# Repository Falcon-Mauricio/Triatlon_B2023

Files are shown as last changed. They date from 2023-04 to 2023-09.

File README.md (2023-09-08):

# Triatlon_B2023

### Indice
[PINOUT PCB](#pinout)<br>
[Normas de convivencia de codigo](#normas)<br>
[Organizacion del repositorio y colaboracion](#colab)<br>
[Imagenes](#imag)<br>

## PINOUT PCB

### Kairimi
```
// Motores
#define M2A 22
#define M2B 23
#define M1B 19
#define M1A 21

// Sensores
#define SENSOR_1 13
#define SENSOR_2 27
#define SENSOR_3 26
#define SENSOR_4 25
#define SENSOR_5 34
#define SENSOR_6 35
#define SENSOR_7 32
#define SENSOR_8 33
#define LEFT_CNY 27
#define RIGHT_CNY 25
#define BACK_CNY 26

// Control
#define BUZZER 18
#define PUSH_1 16
#define PUSH_2 17
```

### C5
```
#define SENSOR_1 13 // left side sharp  
#define SENSOR_2 27 // back cny
#define SENSOR_3 26 // right side sharp
#define SENSOR_4 25 // right cny
#define SENSOR_5 34 // left cny
#define SENSOR_6 35 // left sharp
#define SENSOR_7 32 // center sharp
#define SENSOR_8 33 // right sharp

```
<br>

## Normas de convivencia de codigo

* #### 1.  Convencion de nomenclatura:

    | Tipo      | Caso           | Ejemplo      |
    | :-------: |:--------------:|:------------:|
    | constantes| screaming snake|MAX_READING   |
    | variables | snake case     |color_deadline|
    | objetos   | snake case     |left_sharp    |
    | clases    | pascal case    |Motor         |
    | funciones | pascal case    |ReadFloor     |

* #### 2.  Orden del codigo:

    * Importar librerias
    * Definicion pines
    * Definicion de constantes / variables globales
    * Creacion de clases / objetos (hasta terminar la modularizacion)
    * Funciones globales
    * Velocista
    * Sumo radiocontrolado
    * Despejar area
    * Seleccion de modo / setup / loop
    
* #### 3. Legibilidad:

    * Usar define para los numeros aislados
    * Comentarios descriptivos
    * Codigo limpio y ordenado

<br>

## Organizacion del repositorio y colaboracion

### Arbol de carpetas:

```
├───C5
│   ├───3D
│   ├───CODE
│   └───PCB
├───Kairimi
│   ├───3D
│   ├───CODE
│   └───PCB
├───resources
└───shared
    ├───examples
    └───libs
```

* C5: Dedicado a la version C5 (Rodri/Mauri)

* Kairimi: Dedicado a la version Kairimi (Iris/Julian).
* resources: Librerias externas necesarias para correr el codigo
* shared: Archivos compartidos para los dos robots, como librerias dedicadas

### Colaboracion:

Para colaborar es preferible forkear el repositorio, editar lo necesario en el momento y enviar un pull request. Esto para mantener la actualizacion de archivos ordenada y evitar conflictos entre los robots.

Cuando se alcance una version funcional del robot tagerla marcando las diferencias y mejoras respecto a la anterior y tiempos records de pistas.

<br>

## Imagenes 3Ds / PCBs

### KAIRIMI:

(https://postimg.cc/2q26kCcF)

### C5:

3d en desarrollo.

# Manolos ahi voy 🤤

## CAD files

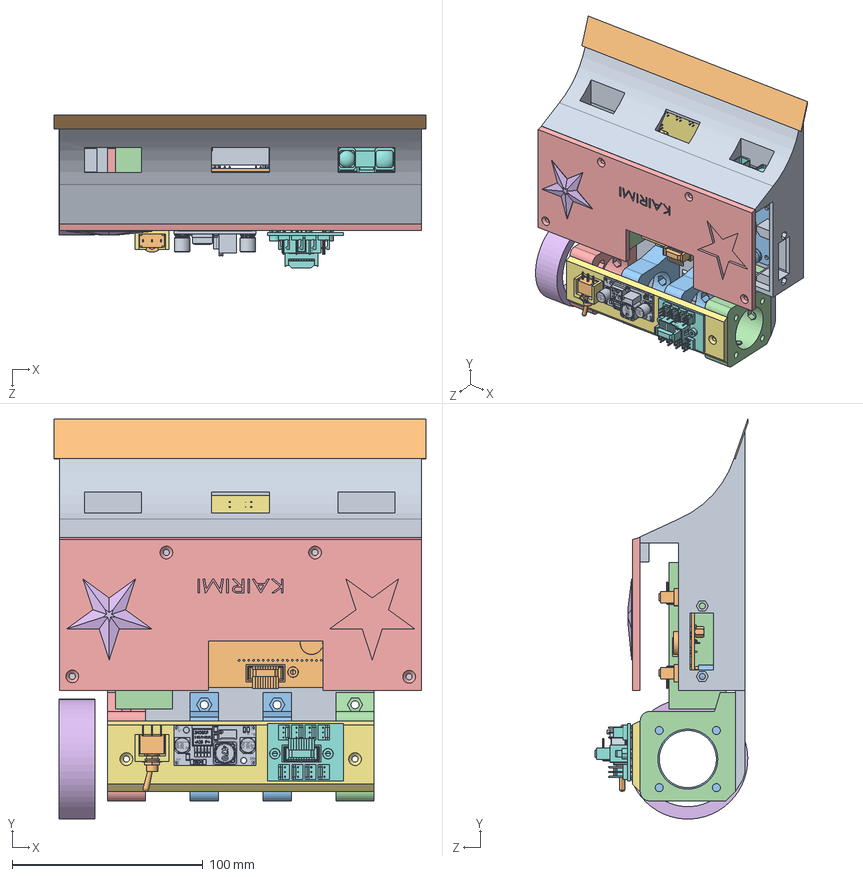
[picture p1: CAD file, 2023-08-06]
C5/3D/Chasis_B2023.SLDASM
195.0 x 209.9 x 80.1 mm
Chasis_B2023_V1
Cuchilla_Fina
Abrazadera_motores_APYS x 2
Soporte_motores_APYS_DER
Soporte_motores_APYS_IZQ
Cubierta_Lisa

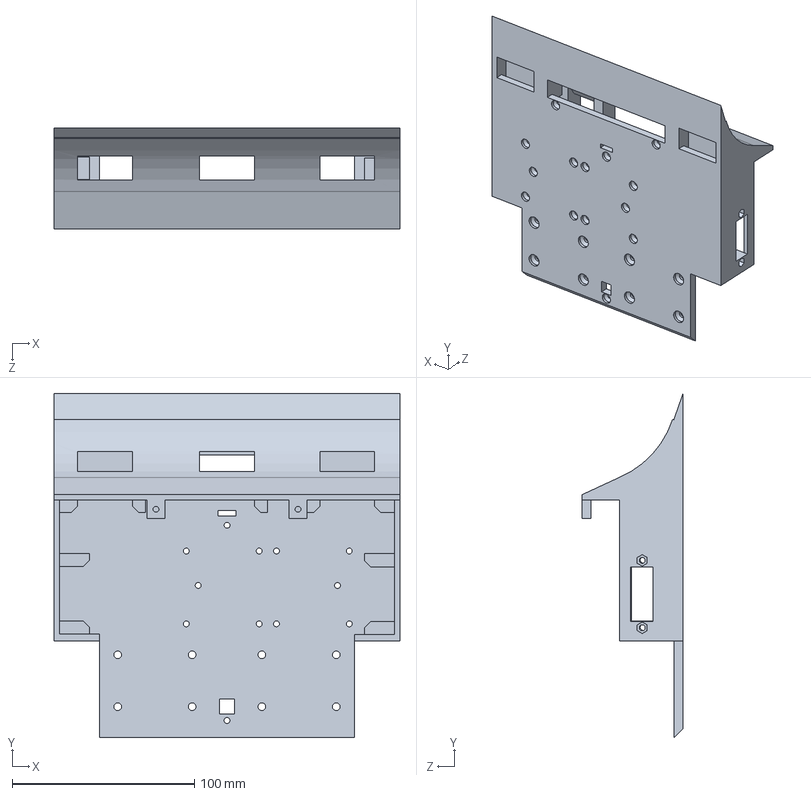
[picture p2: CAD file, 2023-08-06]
C5/3D/Chasis_B2023_V1.SLDPRT
190.0 x 189.1 x 55.5 mm

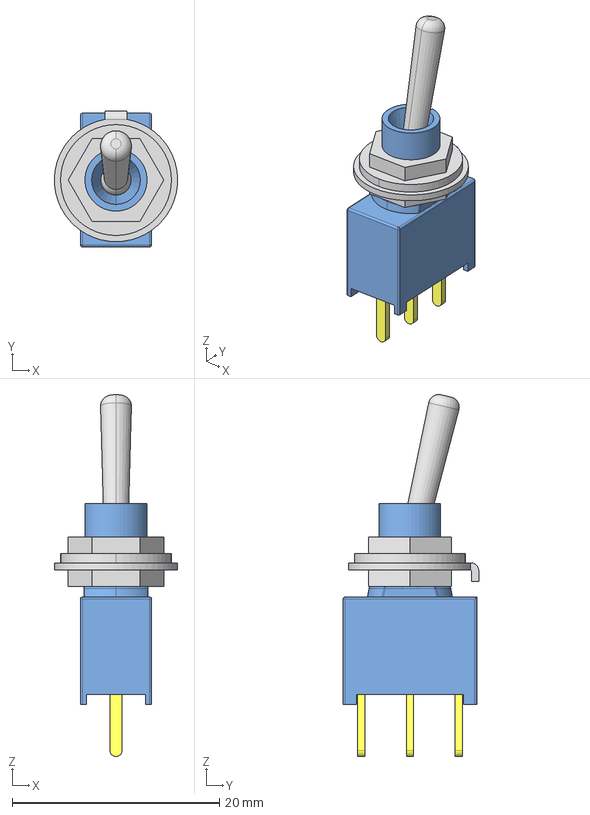
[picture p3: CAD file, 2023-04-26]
C5/3D/Bateria_5V/SW_SPDT_TH_VERTICAL.step
11.9 x 13.1 x 34.9 mm

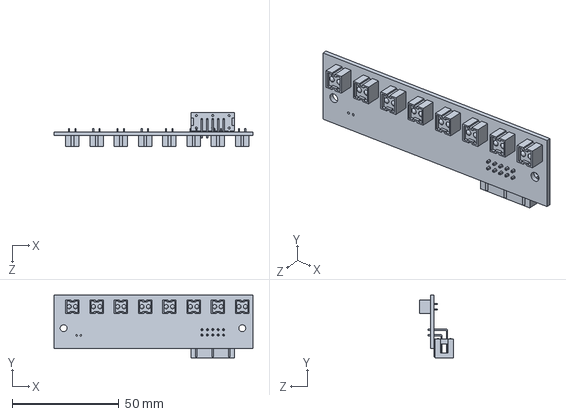
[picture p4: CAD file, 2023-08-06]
C5/3D/PCB_Line_Sensors_x8V2.SLDPRT
93.0 x 29.4 x 16.1 mm

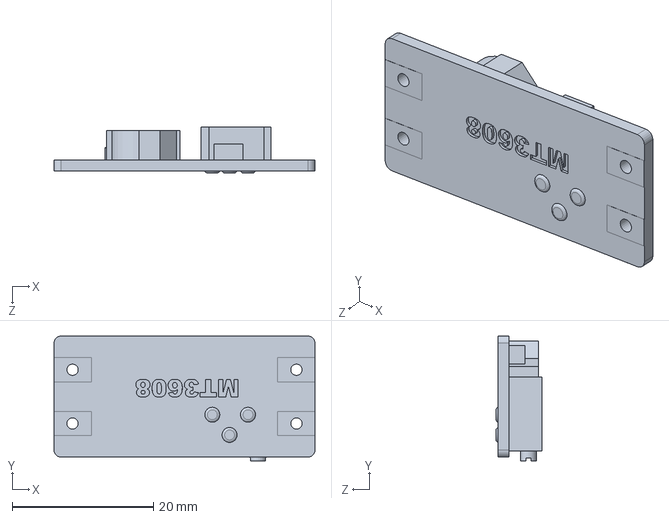
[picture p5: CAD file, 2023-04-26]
C5/3D/Bateria_5V/MT3608_Module_762.SLDPRT
37.0 x 17.7 x 6.50 mm

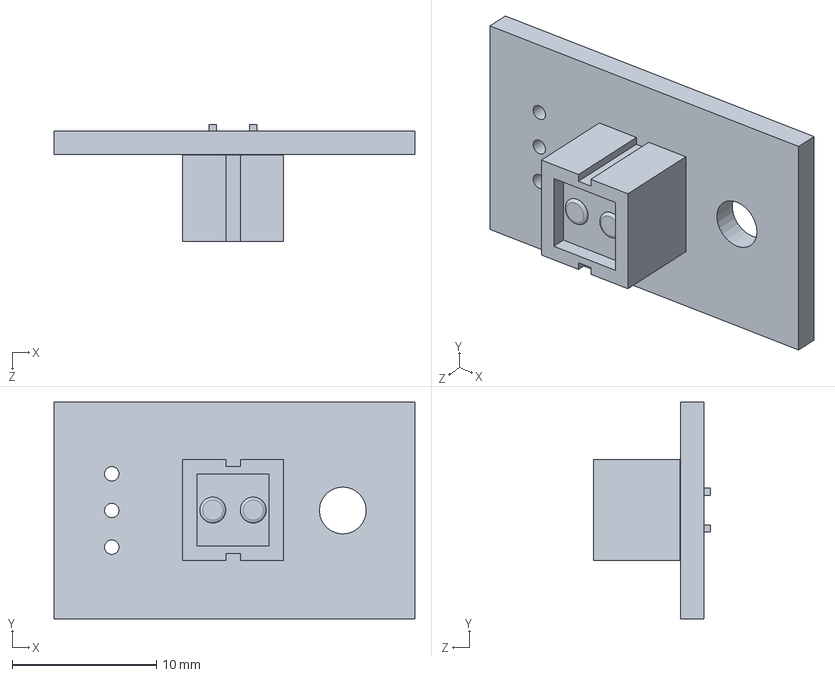
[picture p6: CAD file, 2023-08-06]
C5/3D/PCB_CNY70.SLDPRT
25.0 x 15.0 x 8.12 mm

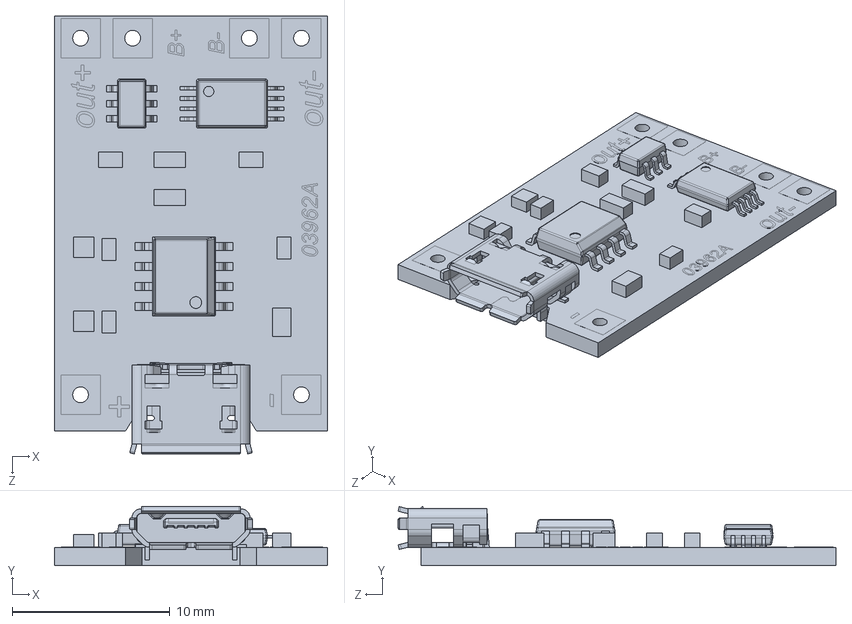
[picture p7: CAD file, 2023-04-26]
C5/3D/Bateria_5V/TP4056.SLDPRT
17.3 x 3.76 x 27.8 mm

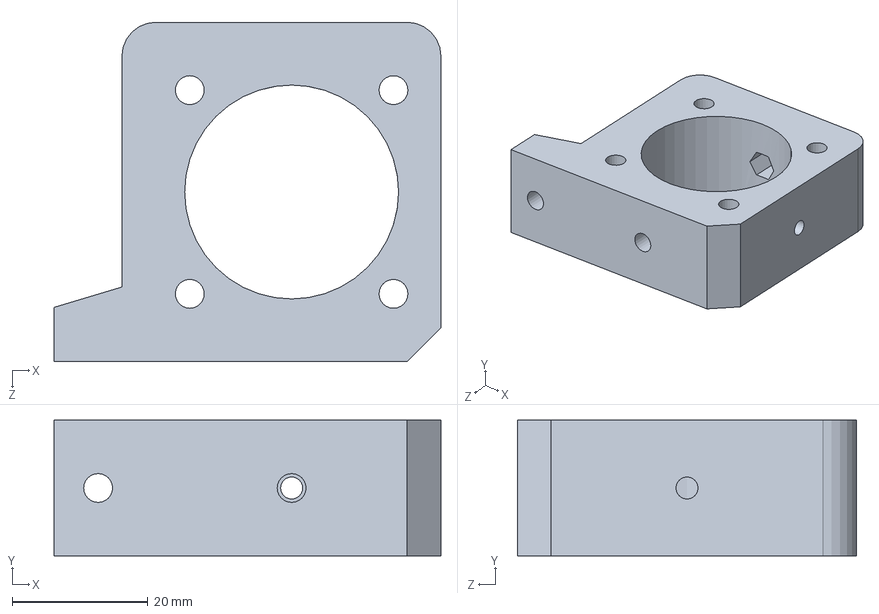
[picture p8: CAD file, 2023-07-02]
C5/3D/Soporte_motores_APYS_IZQ.SLDPRT
57.0 x 20.0 x 50.0 mm

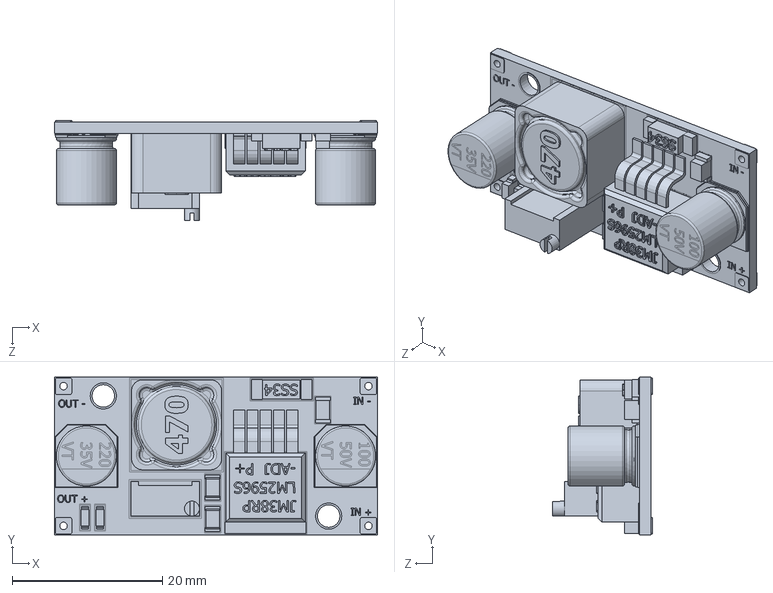
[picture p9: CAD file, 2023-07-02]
C5/3D/lm2596.SLDPRT
43.0 x 21.0 x 13.4 mm

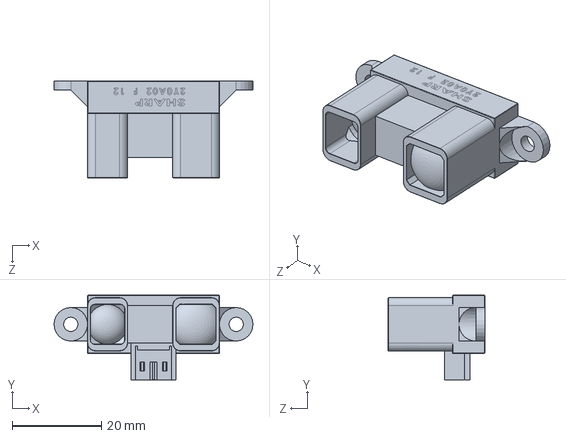
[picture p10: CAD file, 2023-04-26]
C5/3D/GP2Y0A02YK0F_SHARP.SLDPRT
44.5 x 18.9 x 21.6 mm

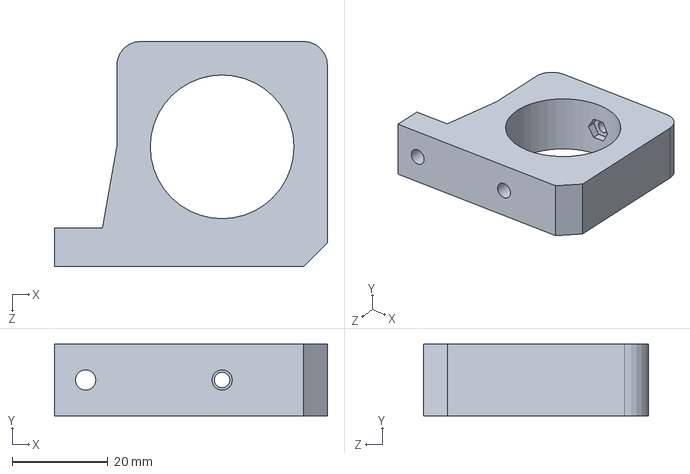
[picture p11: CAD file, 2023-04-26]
C5/3D/Abrazadera_motores_APYS.SLDPRT
57.0 x 15.0 x 47.0 mm

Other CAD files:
C5/3D/Bateria_5V/Base_5v_usb.SLDPRT
C5/3D/Tapa_B2023.SLDPRT
C5/3D/Estrella_Tapa.SLDPRT
C5/3D/Soporte_Alimentacion.SLDPRT
C5/3D/Soporte_SensorMedio.SLDPRT
C5/3D/Cubierta_Lisa.SLDPRT
C5/3D/Soporte_motores_APYS_DER.SLDPRT
C5/3D/BTS7960.SLDPRT
C5/3D/Bateria 4s.SLDPRT
C5/3D/Bateria_5V/18650_Holder.SLDPRT
C5/3D/Cuchilla_Fina.SLDPRT

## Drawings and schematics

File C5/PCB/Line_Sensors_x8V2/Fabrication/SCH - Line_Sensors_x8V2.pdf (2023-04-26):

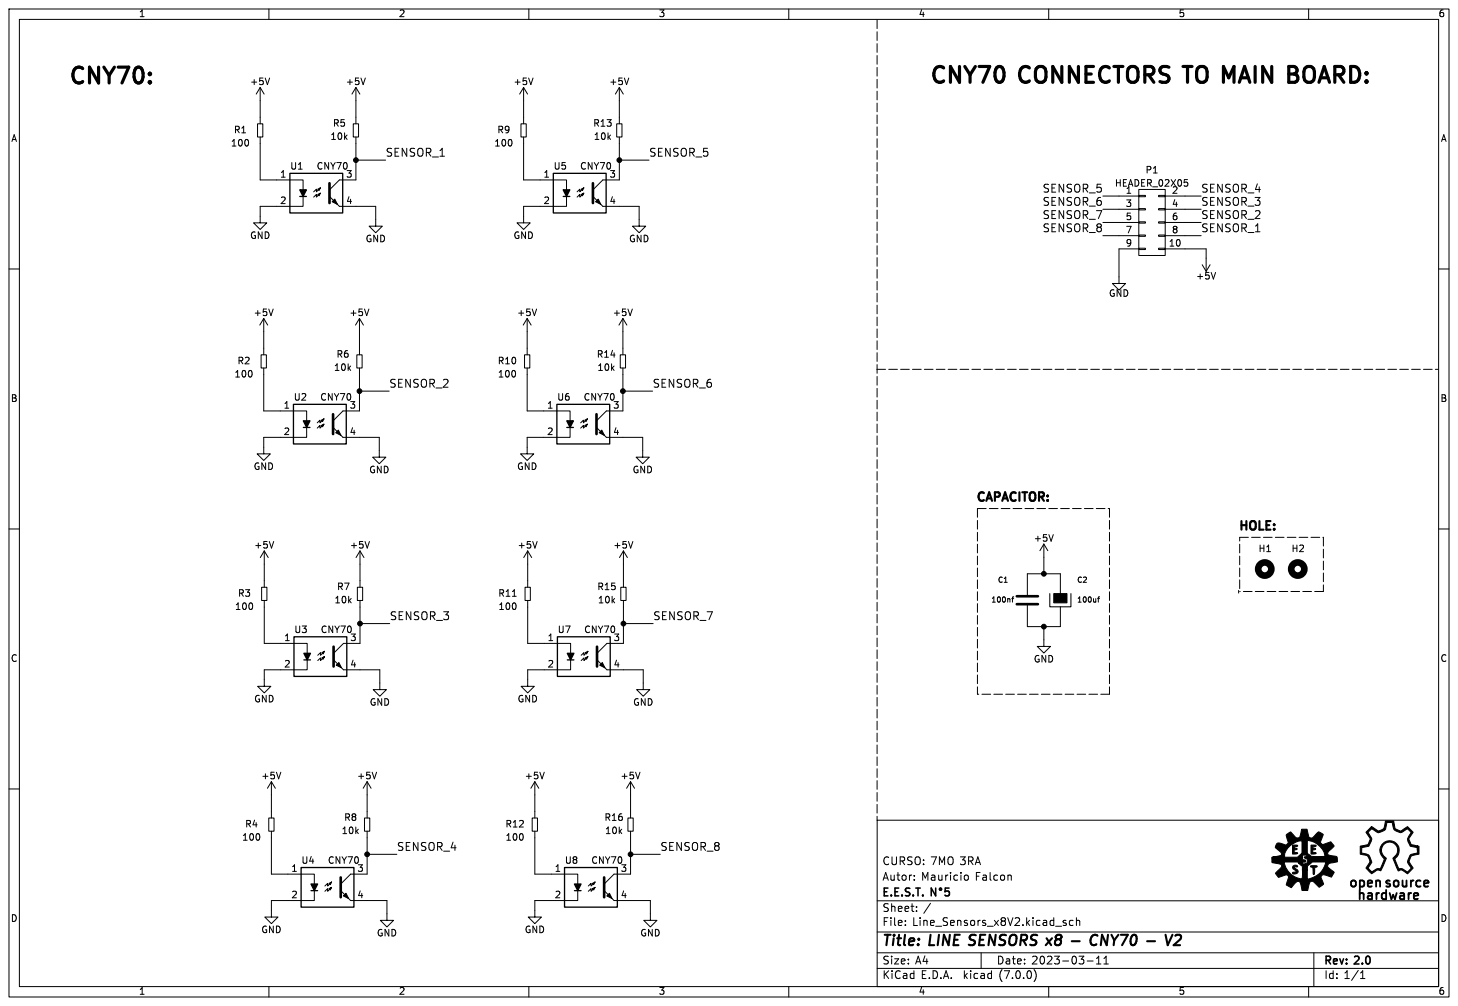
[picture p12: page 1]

CNY70 CONNECTORS TO MAIN BOARD:

Id: 1/1 Title: LINE SENSORS x8 - CNY70 - V2

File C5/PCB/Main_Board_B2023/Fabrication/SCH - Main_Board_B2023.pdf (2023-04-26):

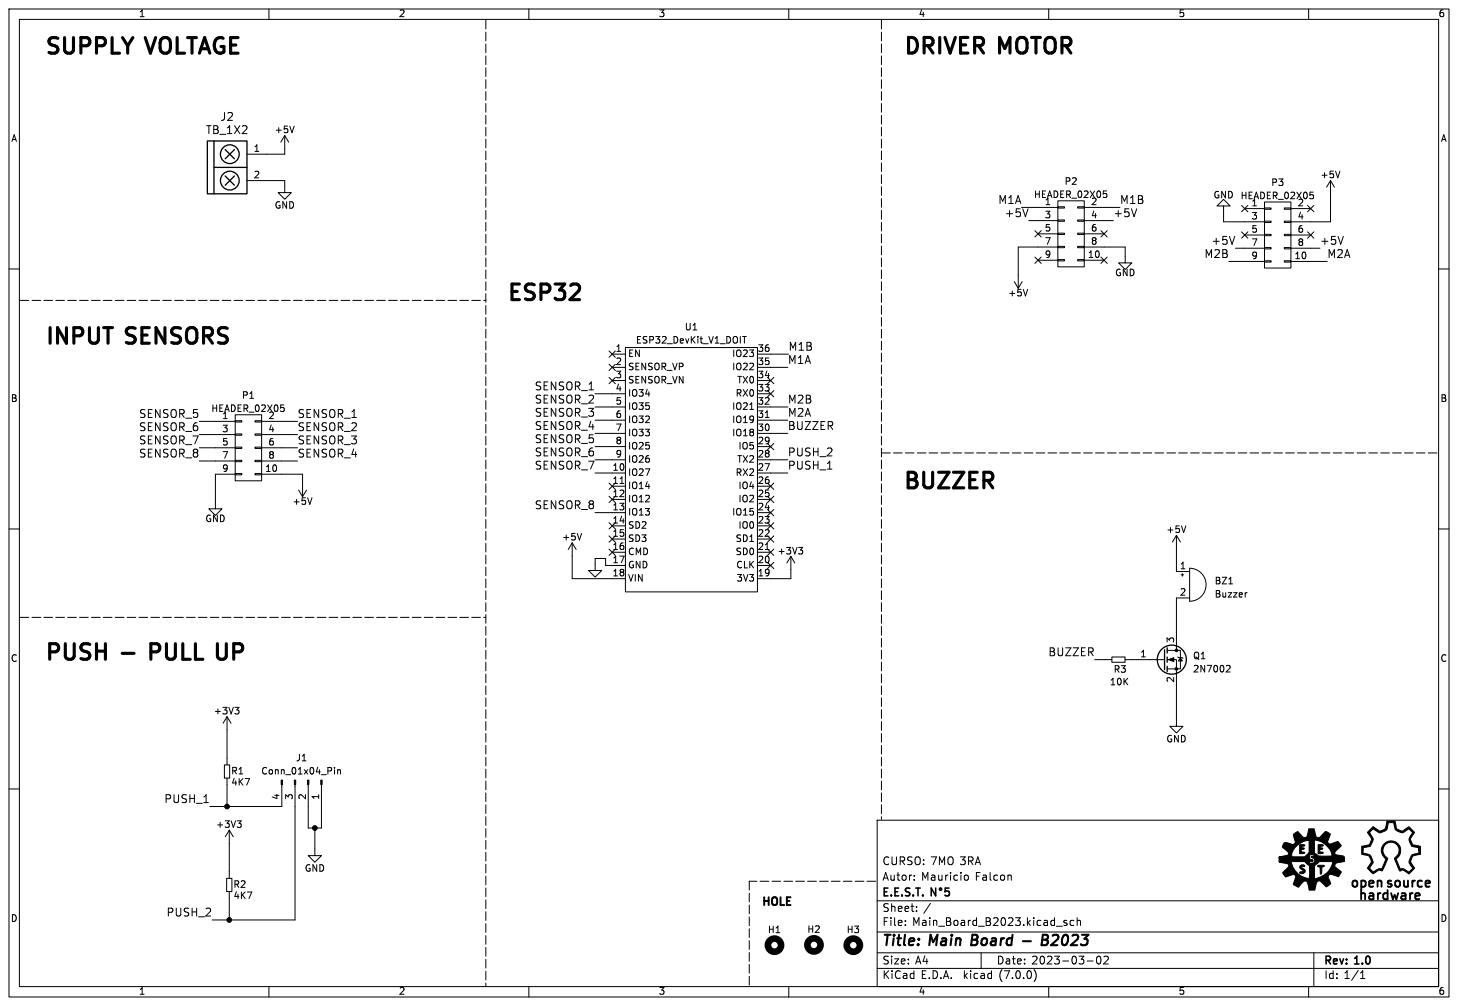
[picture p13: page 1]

Id: 1/1 Title: Main Board - B2023

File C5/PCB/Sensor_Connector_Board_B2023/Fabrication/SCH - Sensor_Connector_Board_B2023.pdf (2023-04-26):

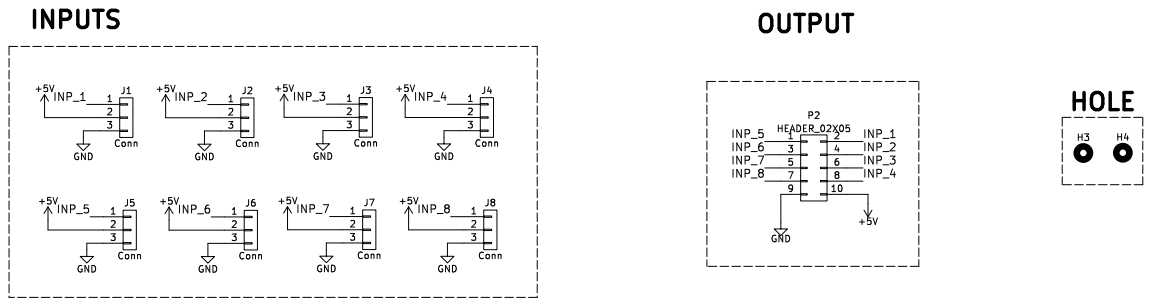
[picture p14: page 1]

Id: 1/1 Title: Sensor Connector Board - B2023

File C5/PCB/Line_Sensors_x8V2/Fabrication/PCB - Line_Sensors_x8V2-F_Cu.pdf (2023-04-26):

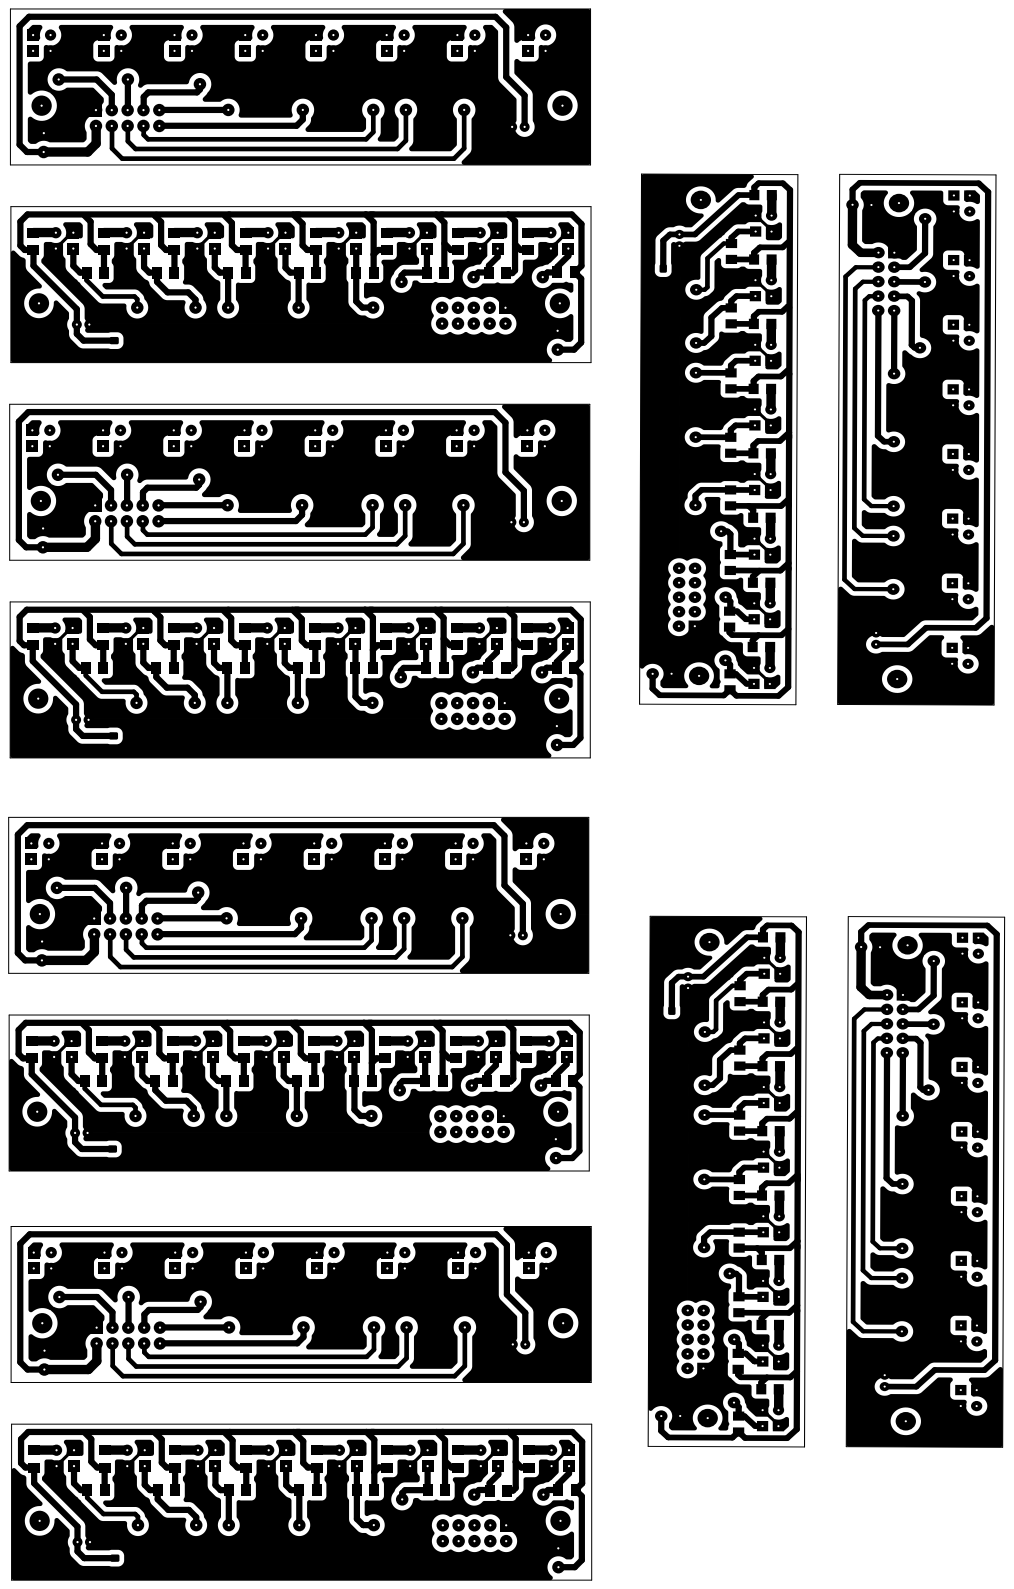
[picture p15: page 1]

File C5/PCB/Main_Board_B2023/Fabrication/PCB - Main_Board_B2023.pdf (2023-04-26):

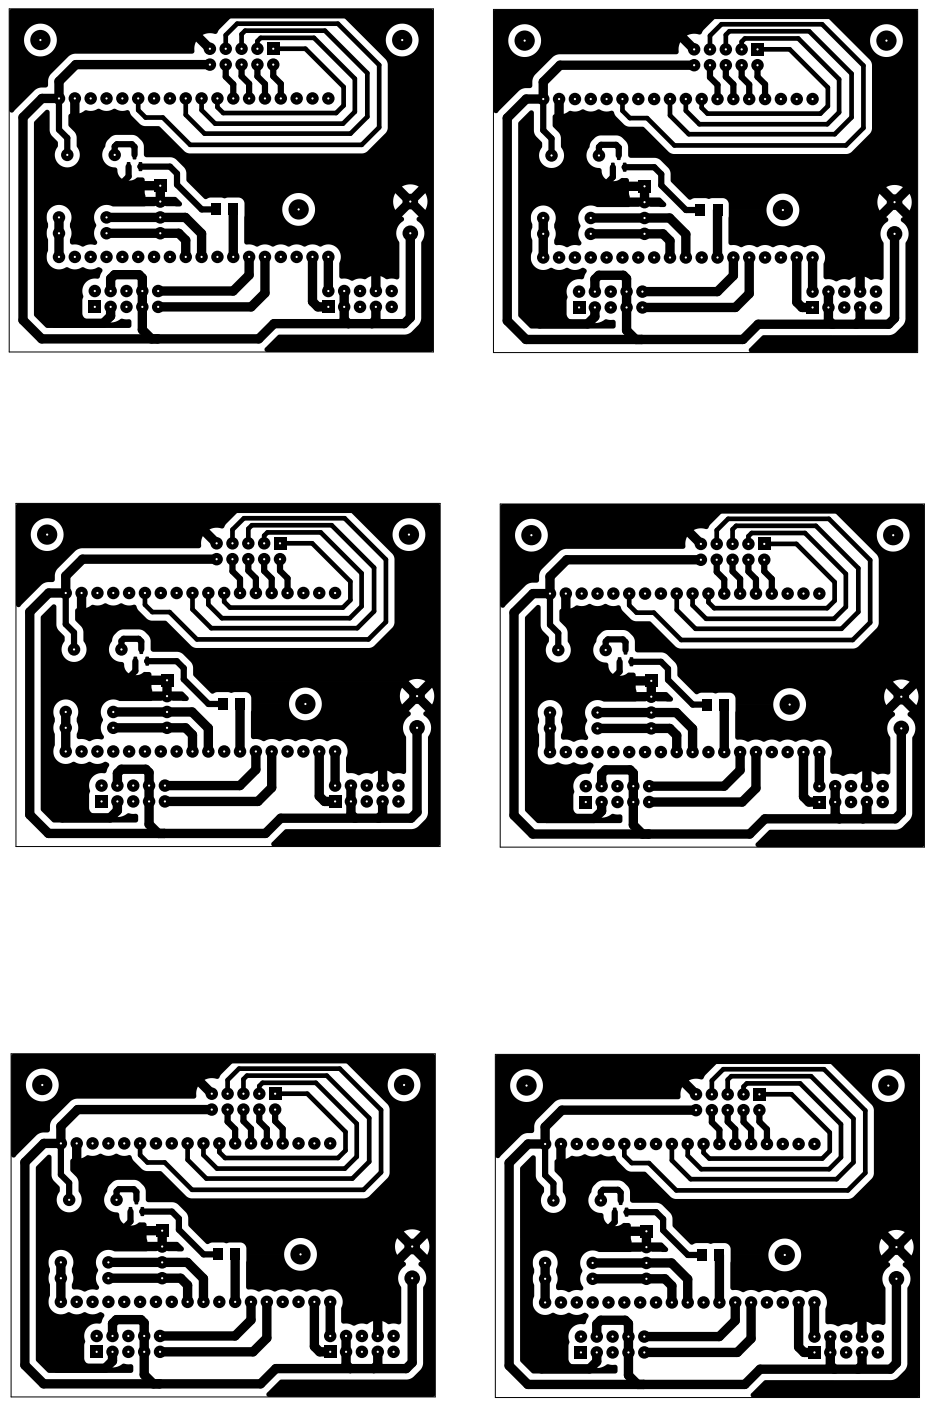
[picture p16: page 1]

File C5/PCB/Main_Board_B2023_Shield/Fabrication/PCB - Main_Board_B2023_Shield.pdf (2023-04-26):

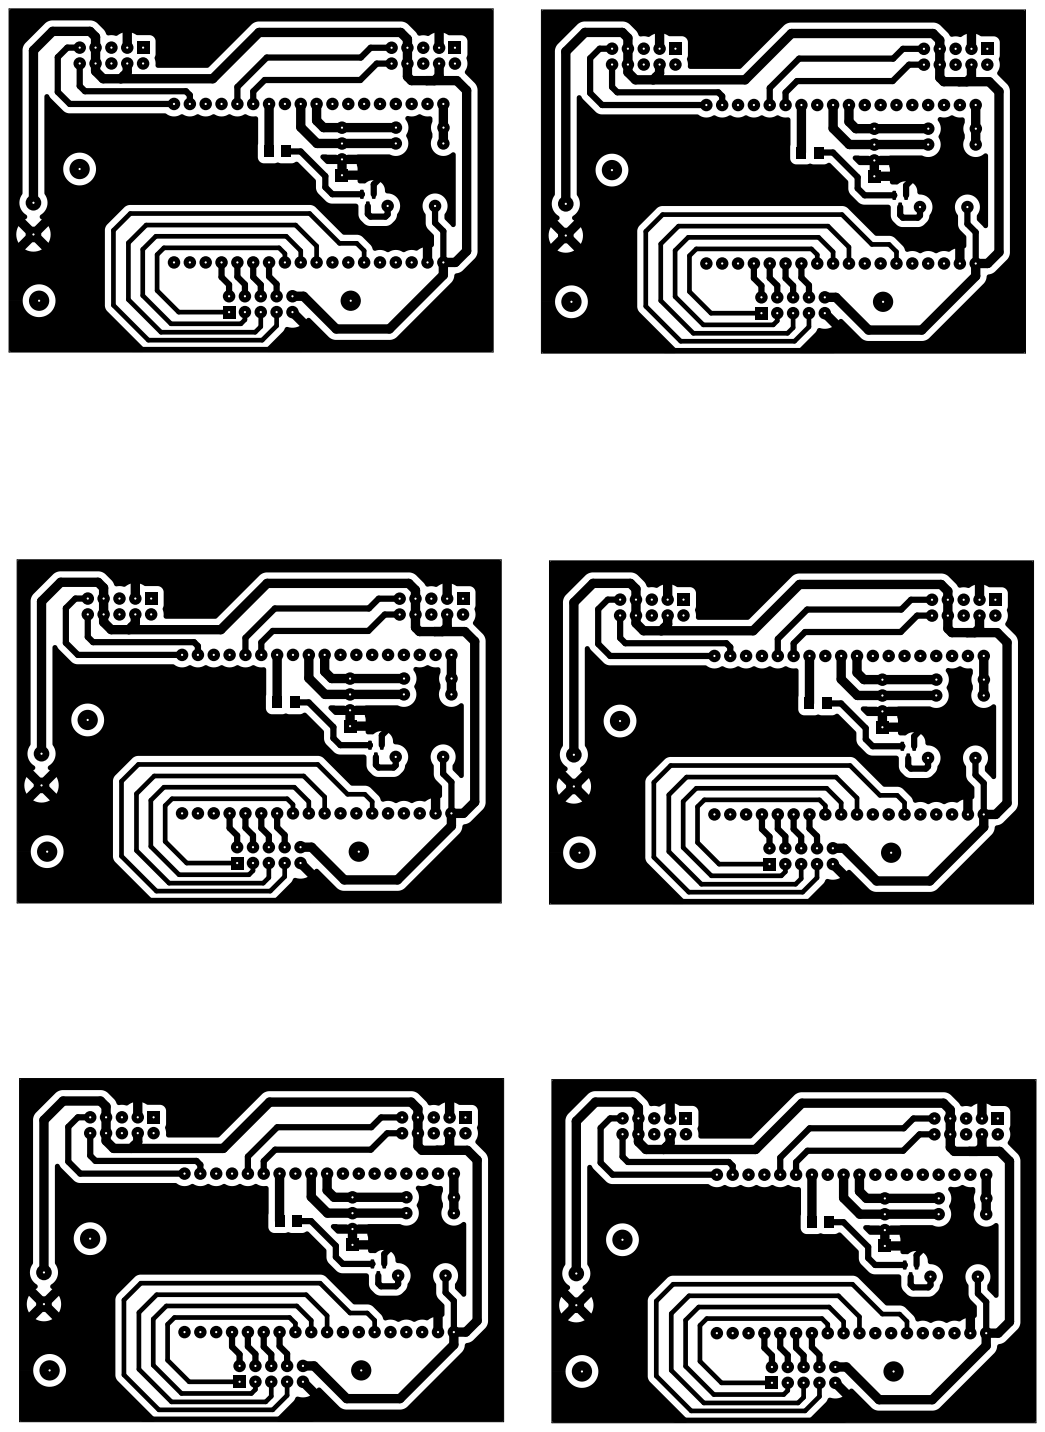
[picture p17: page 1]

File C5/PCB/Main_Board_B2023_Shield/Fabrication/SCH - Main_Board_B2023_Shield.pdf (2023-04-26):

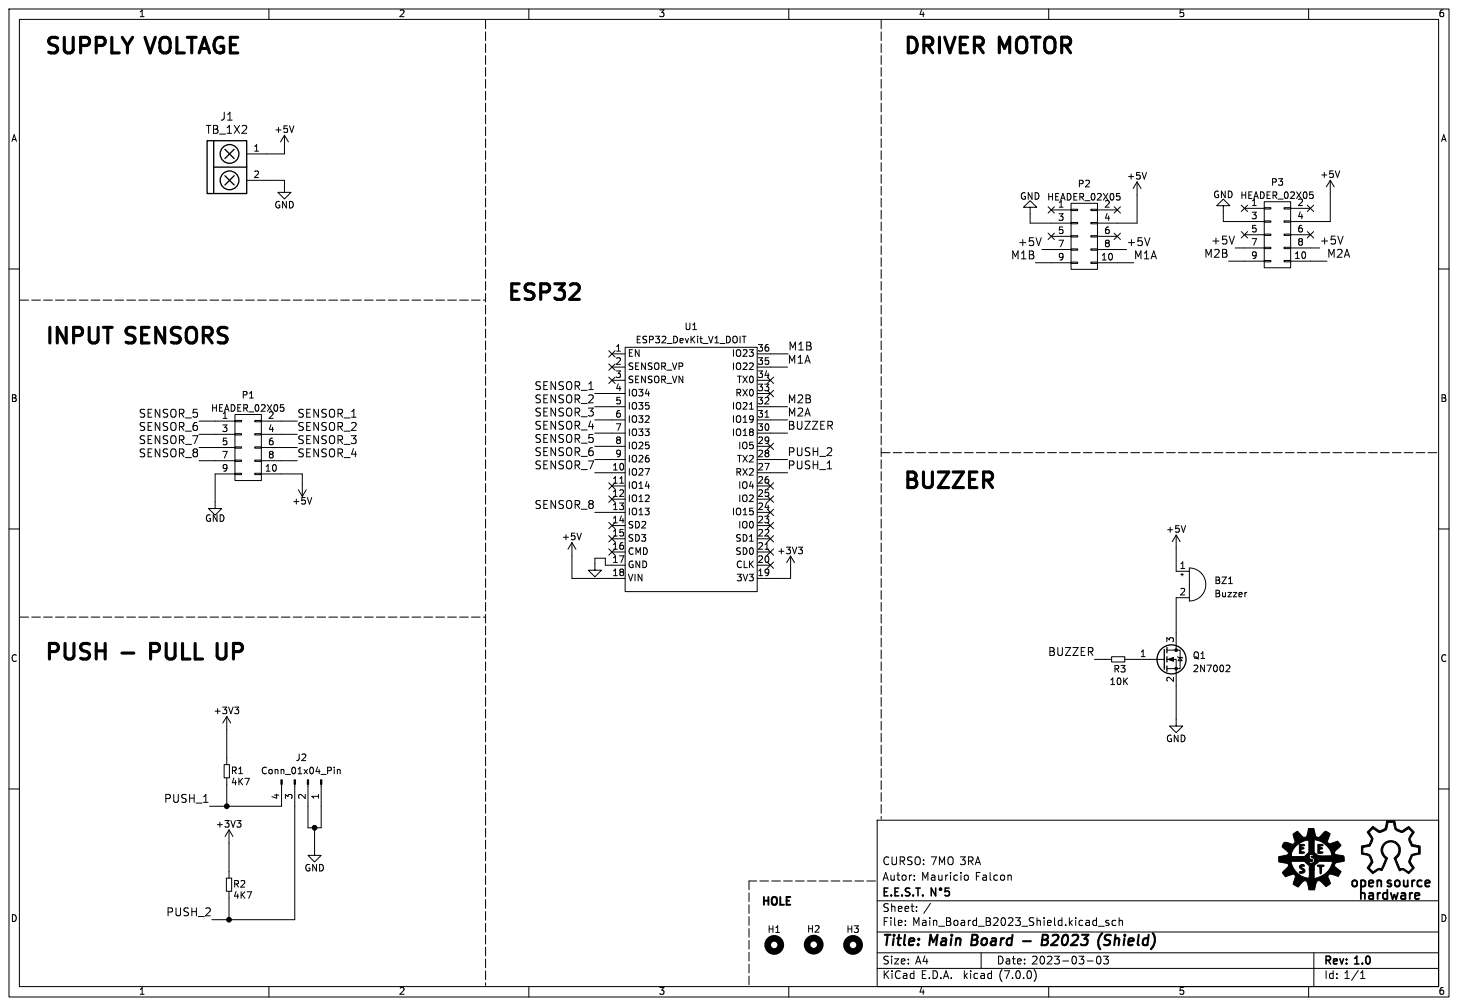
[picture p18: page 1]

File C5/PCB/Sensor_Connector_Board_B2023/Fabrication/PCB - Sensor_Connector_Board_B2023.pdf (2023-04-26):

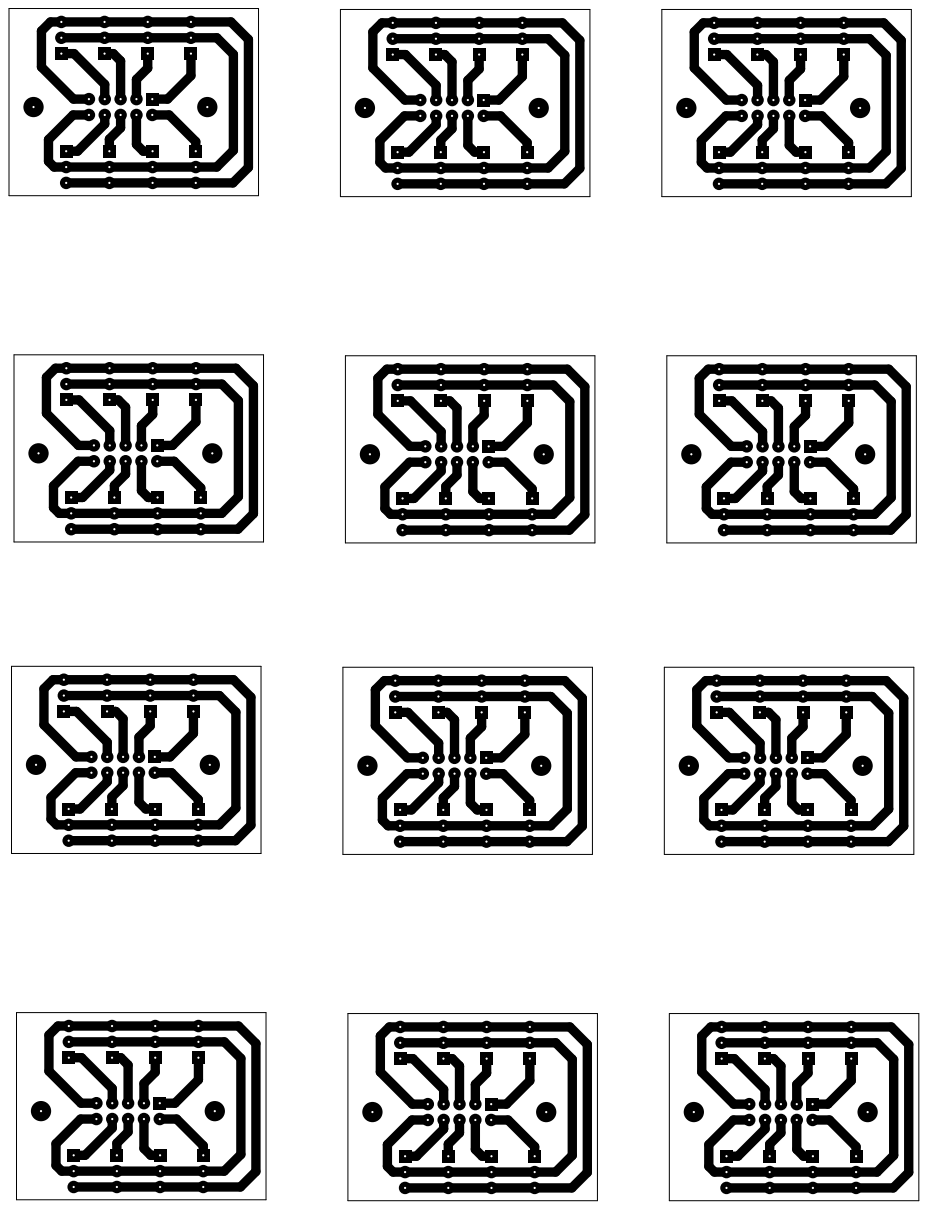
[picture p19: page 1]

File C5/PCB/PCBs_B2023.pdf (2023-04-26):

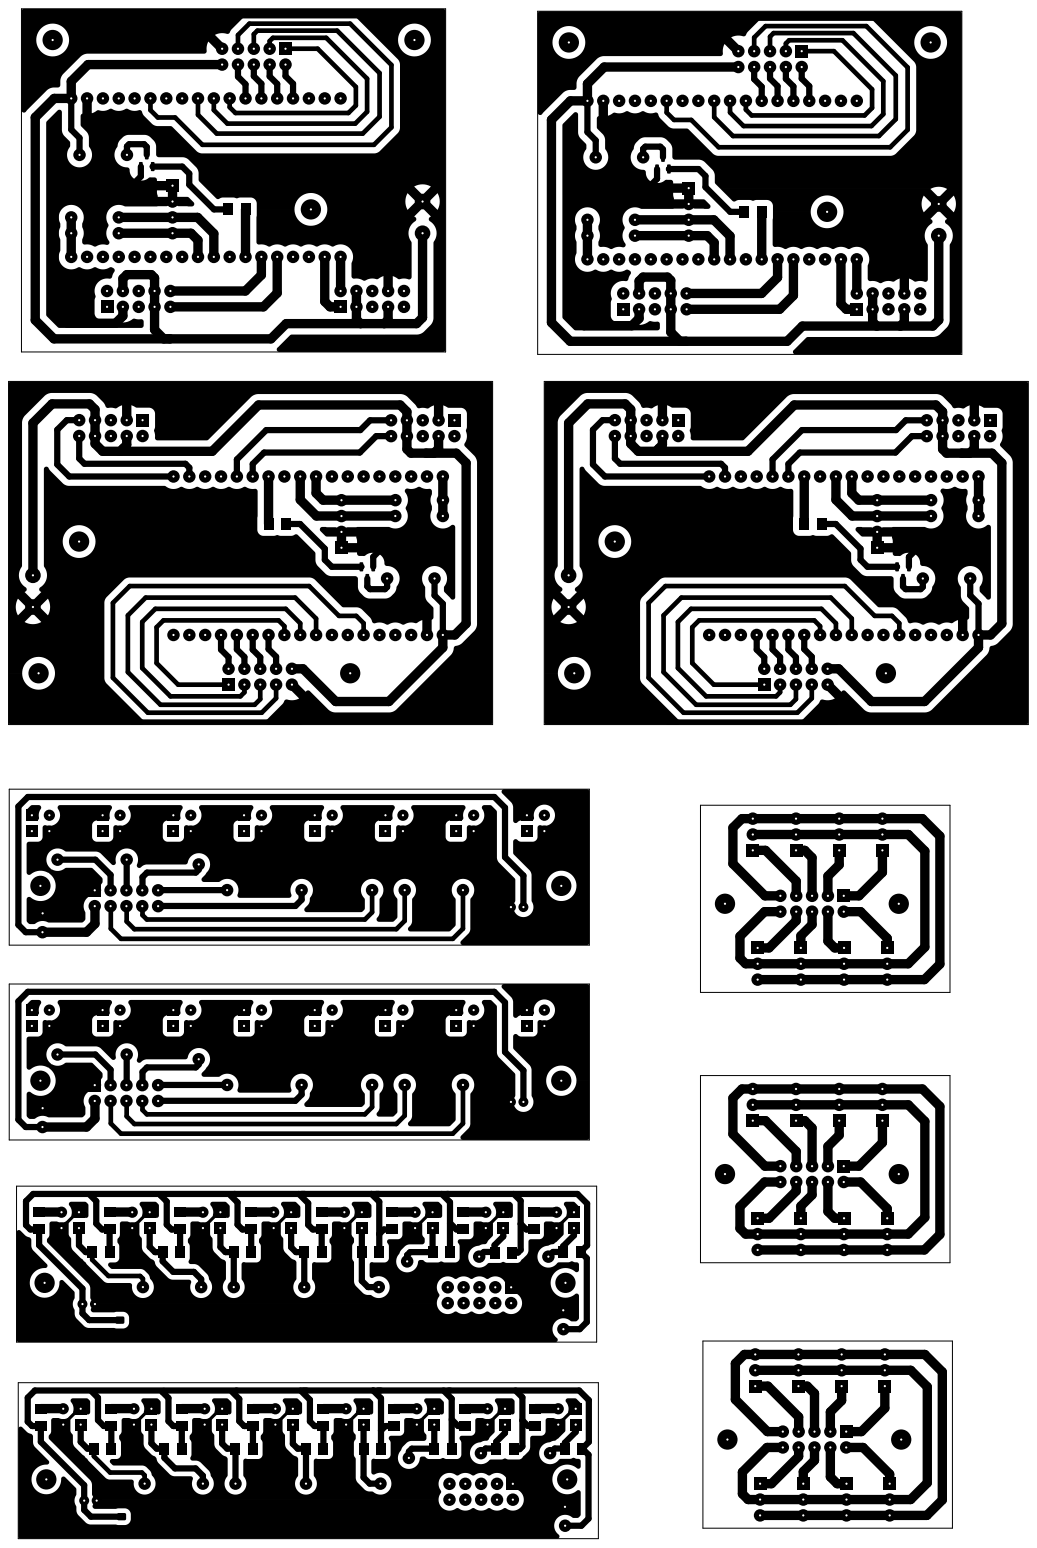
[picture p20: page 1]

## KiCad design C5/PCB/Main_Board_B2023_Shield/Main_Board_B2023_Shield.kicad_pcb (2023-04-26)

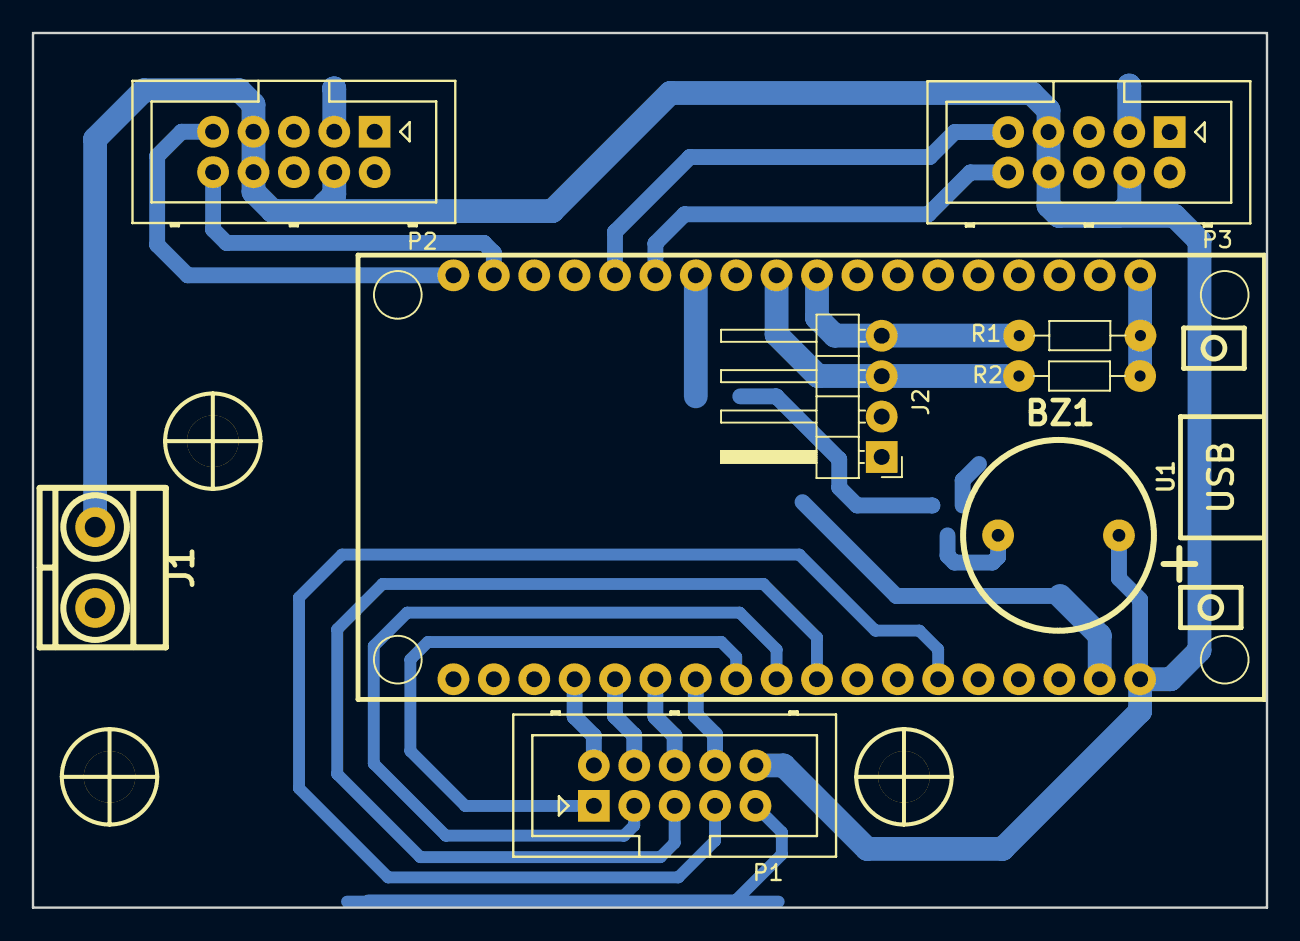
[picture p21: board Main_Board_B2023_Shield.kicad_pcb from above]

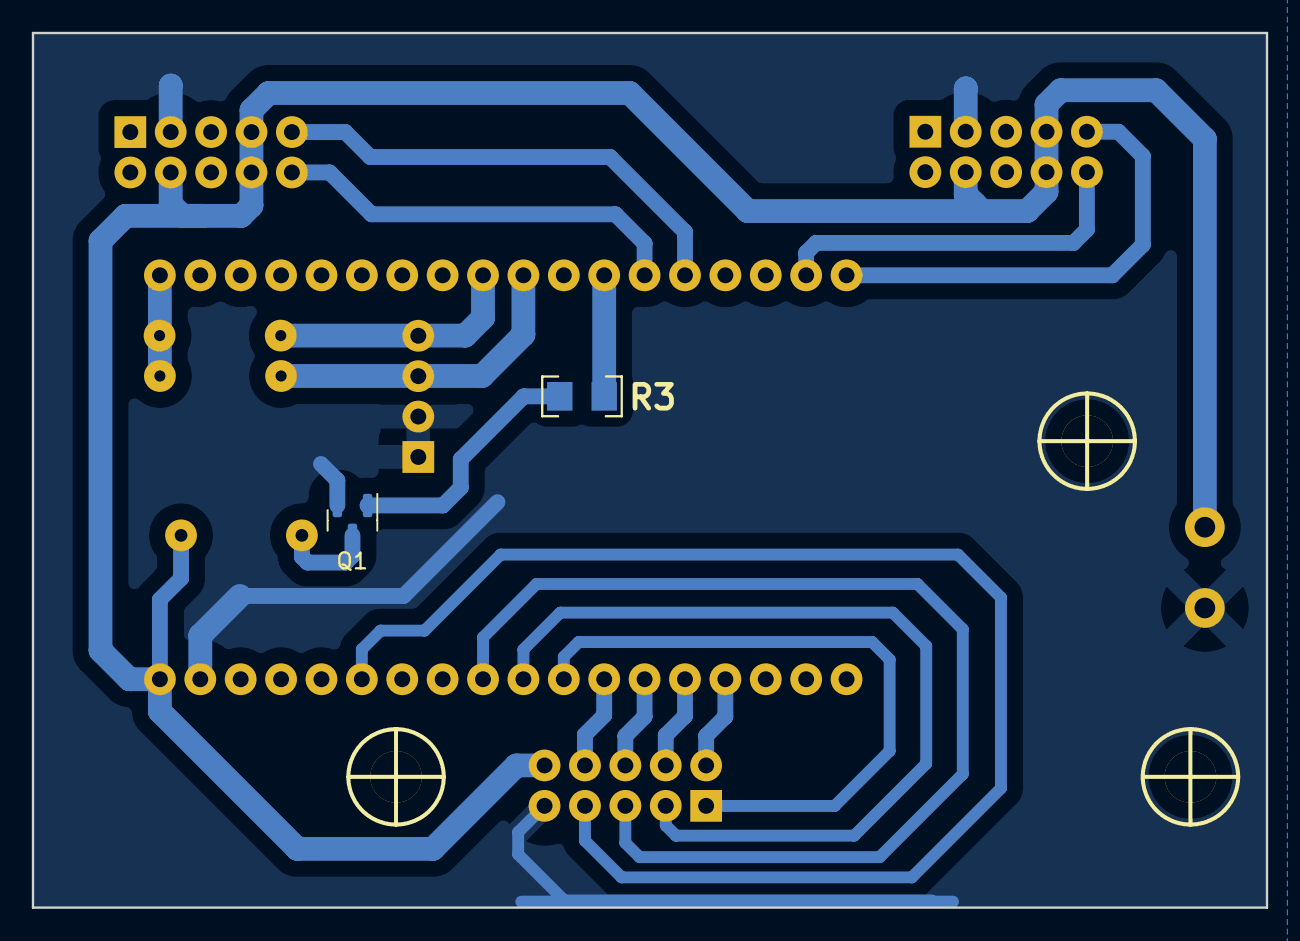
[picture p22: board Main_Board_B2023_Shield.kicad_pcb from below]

Board: 2 copper layers, 77.6 x 55.0 mm, 14 parts (2 on the bottom side), 20 nets.

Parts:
BZ1: Buzzer; Buzzer_12mm
H1, H2, H3: Mounting_Hole; Separador_M3_5mm
J1: TB_1X2; BORNERA2_AZUL
J2: Conn_01x04_Pin; PinHeader_1x04_P2.54mm_Horizontal
P1, P2, P3: HEADER_02X05; Header_2x05x2.54mm_Vertical
Q1: 2N7002; SOT-23
R1, R2: 4K7; R_Axial_DIN0204_L3.6mm_D1.6mm_P7.62mm_Horizontal
R3: 10K; R_1206
U1: ESP32_DevKit_V1_DOIT; ESP32_DEVKIT_V1_DOIT

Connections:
+3V3: R1.1, R2.1, U1.19 (3V3)
+5V: BZ1.1 (-), J1.1, P1.10, P2.4, P2.7, P2.8, P3.4, P3.7, P3.8, U1.18 (VIN)
/BUZZER: R3.2, U1.30 (IO18)
/M1A: P2.10, U1.35 (IO22)
/M1B: P2.9, U1.36 (IO23)
/M2A: P3.10, U1.31 (IO19)
/M2B: P3.9, U1.32 (IO21)
/PUSH_1: J2.4, R1.2, U1.27 (RX2)
/PUSH_2: J2.3, R2.2, U1.28 (TX2)
/SENSOR_1: P1.2, U1.4 (IO34)
/SENSOR_2: P1.4, U1.5 (IO35)
/SENSOR_3: P1.6, U1.6 (IO32)
/SENSOR_4: P1.8, U1.7 (IO33)
/SENSOR_5: P1.1, U1.8 (IO25)
/SENSOR_6: P1.3, U1.9 (IO26)
/SENSOR_7: P1.5, U1.10 (IO27)
/SENSOR_8: P1.7, U1.13 (IO13)
GND: J1.2, J2.1, J2.2, P1.9, P2.3, P3.3, Q1.2 (S), U1.17 (GND)
unnamed: BZ1.2 (+), Q1.3 (D)
unnamed: Q1.1 (G), R3.1

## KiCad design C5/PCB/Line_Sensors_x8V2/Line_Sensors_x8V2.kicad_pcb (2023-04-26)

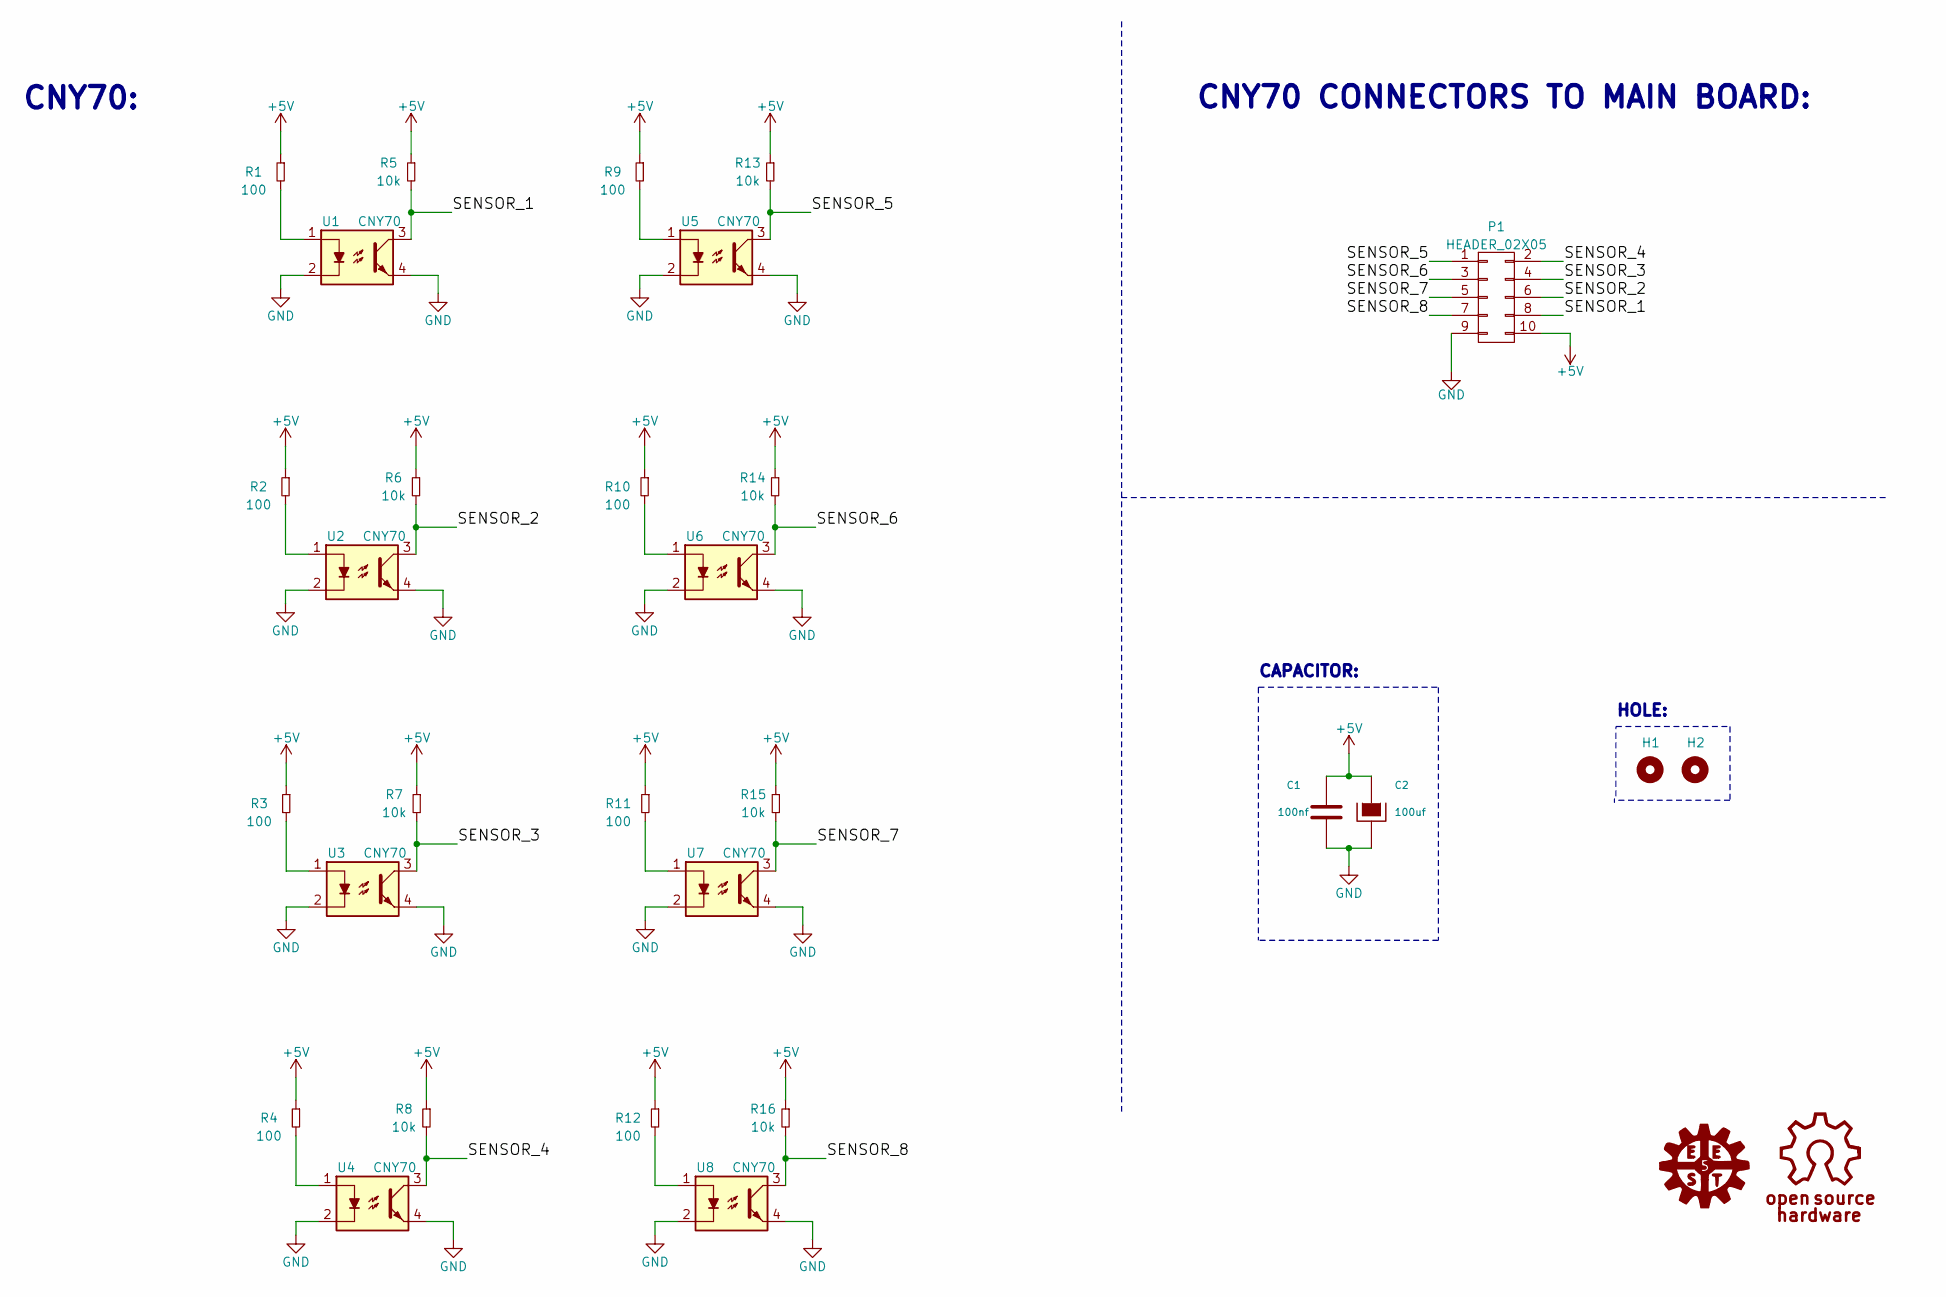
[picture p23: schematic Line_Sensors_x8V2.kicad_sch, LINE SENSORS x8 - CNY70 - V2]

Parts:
C1: 100nf; C_0805_2012Metric_Pad1.18x1.45mm_HandSolder
C2: 100uf; C_Radial_D5.0mm_H11.0mm_P2.00mm
H1, H2: HOLE; Separador_M3_5mm
P1: HEADER_02X05; Header_2x05x2.54mm_Vertical
R1, R2, R3, R4, R9, R10, R11, R12: 100; R_1206
R5, R6, R7, R8, R13, R14, R15, R16: 10k; R_1206
U1, U2, U3, U4, U5, U6, U7, U8: CNY70

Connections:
+5V: C1.1, C2.1, P1.10, R1.1, R2.1, R3.1, R4.1, R5.1, R6.1, R7.1, R8.1, R9.1, R10.1, R11.1, R12.1, R13.1, R14.1, R15.1, R16.1
/SENSOR_1: P1.8, R5.2, U1.3
/SENSOR_2: P1.6, R6.2, U2.3
/SENSOR_3: P1.4, R7.2, U3.3
/SENSOR_4: P1.2, R8.2, U4.3
/SENSOR_5: P1.1, R13.2, U5.3
/SENSOR_6: P1.3, R14.2, U6.3
/SENSOR_7: P1.5, R15.2, U7.3
/SENSOR_8: P1.7, R16.2, U8.3
GND: C1.2, C2.2, P1.9, U1.2, U1.4, U2.2, U2.4, U3.2, U3.4, U4.2, U4.4, U5.2, U5.4, U6.2, U6.4, U7.2, U7.4, U8.2, U8.4
unnamed: R1.2, U1.1
unnamed: R2.2, U2.1
unnamed: R3.2, U3.1
unnamed: R4.2, U4.1
unnamed: R9.2, U5.1
unnamed: R10.2, U6.1
unnamed: R11.2, U7.1
unnamed: R12.2, U8.1

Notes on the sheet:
CNY70 CONNECTORS TO MAIN BOARD:
CAPACITOR:
CNY70:
HOLE:

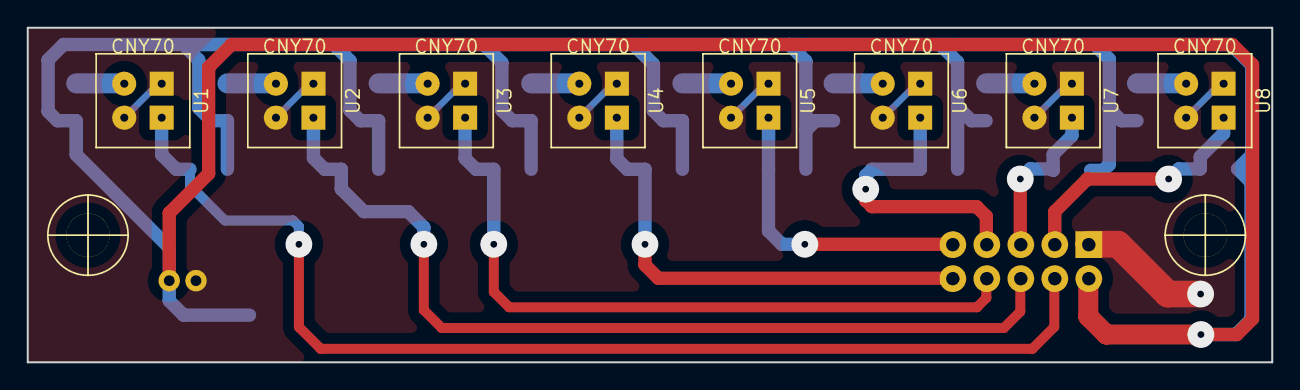
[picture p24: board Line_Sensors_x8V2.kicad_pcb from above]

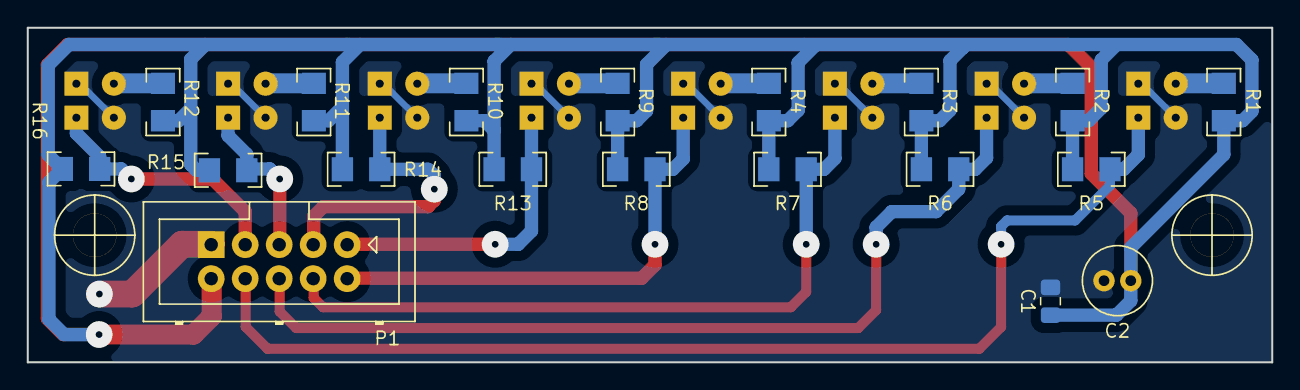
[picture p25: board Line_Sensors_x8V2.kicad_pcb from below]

Board: 2 copper layers, 93.0 x 25.0 mm, 29 parts (21 on the bottom side), 18 nets.

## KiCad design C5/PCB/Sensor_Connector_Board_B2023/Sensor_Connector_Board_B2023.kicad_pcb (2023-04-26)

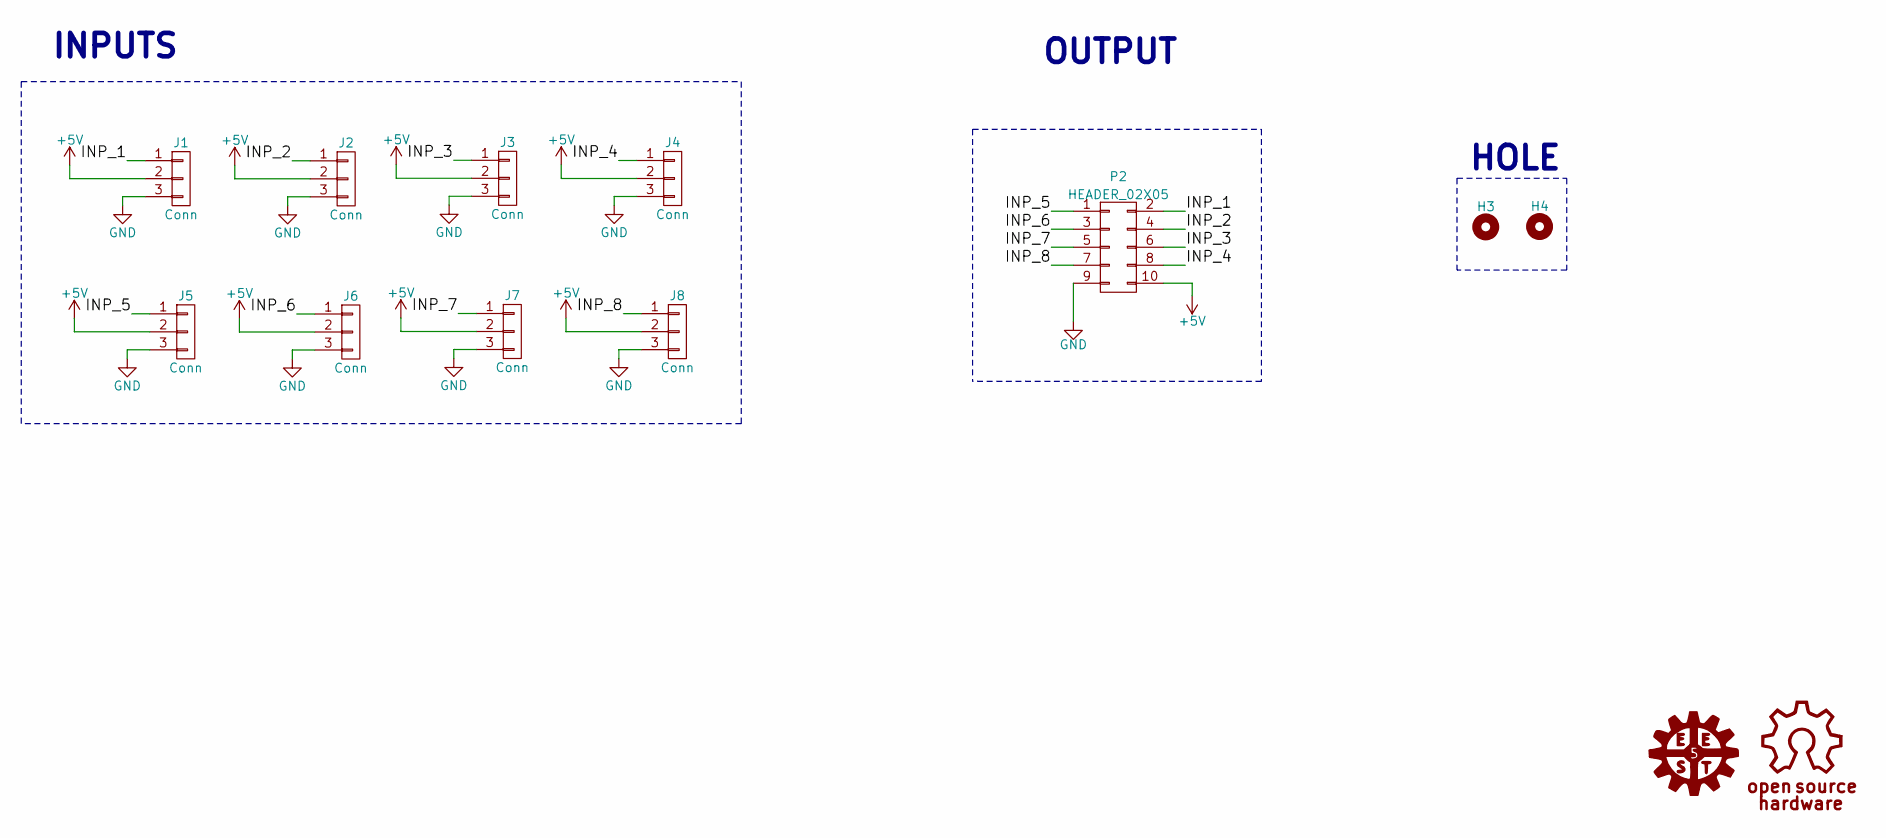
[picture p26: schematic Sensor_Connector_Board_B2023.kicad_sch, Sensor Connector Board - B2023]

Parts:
H3, H4: Mounting_Hole; Separador_M3_5mm
J1, J2, J3, J4, J5, J6, J7, J8: Conn; FanPinHeader_1x03_P2.54mm_Vertical
P2: HEADER_02X05; Header_2x05x2.54mm_Vertical

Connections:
+5V: J1.2, J2.2, J3.2, J4.2, J5.2, J6.2, J7.2, J8.2, P2.10
/INP_1: J1.1, P2.2
/INP_2: J2.1, P2.4
/INP_3: J3.1, P2.6
/INP_4: J4.1, P2.8
/INP_5: J5.1, P2.1
/INP_6: J6.1, P2.3
/INP_7: J7.1, P2.5
/INP_8: J8.1, P2.7
GND: J1.3, J2.3, J3.3, J4.3, J5.3, J6.3, J7.3, J8.3, P2.9

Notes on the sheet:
INPUTS
HOLE
OUTPUT

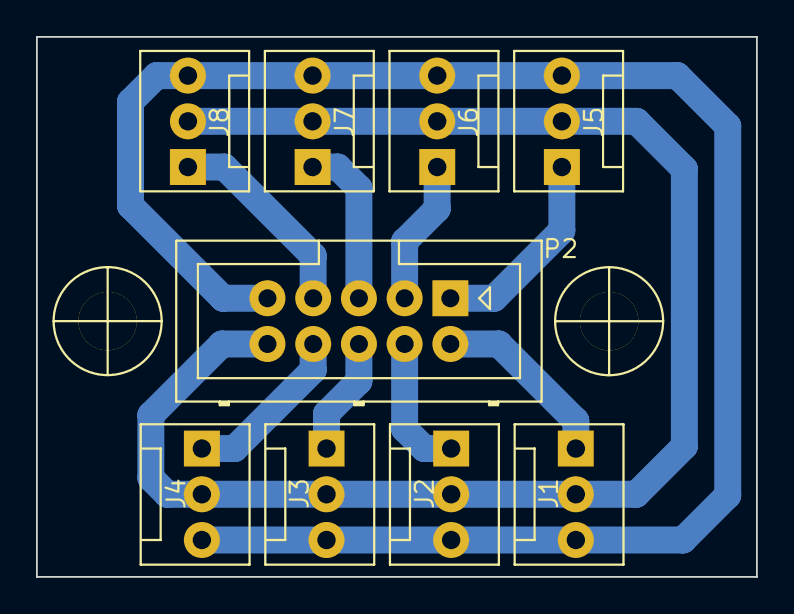
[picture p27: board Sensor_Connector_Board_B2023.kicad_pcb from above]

Board: 2 copper layers, 40.0 x 30.0 mm, 11 parts (0 on the bottom side), 10 nets.

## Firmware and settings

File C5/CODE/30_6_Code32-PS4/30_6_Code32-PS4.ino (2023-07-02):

#include <PS4Controller.h>

#include <BluetoothSerial.h>

#define DEBUG 1
// Motores
#define M2A 22
#define M2B 23
#define M1B 19
#define M1A 21

// Sensores
#define SENSOR_1 13
#define SENSOR_2 27
#define SENSOR_3 26
#define SENSOR_4 25
#define SENSOR_5 34
#define SENSOR_6 35
#define SENSOR_7 32
#define SENSOR_8 33
#define left_CNY 27
#define right_CNY 25

int Cny70_pins[] = { SENSOR_1, SENSOR_2, SENSOR_3, SENSOR_4, SENSOR_5, SENSOR_6, SENSOR_7, SENSOR_8 };

#define CNY70_CANT 8

// Control
#define BUZZER 18
#define PUSH_1 16
#define PUSH_2 17

// Constantes

#define BLACK 1
#define WHITE 0
#define YES 1
#define NO 0
#define LEFT 1
#define RIGHT 0

int black_side = BLACK;

class Buzzer {

private:
  int pin;

public:
  Buzzer(int pin);
  void Use(int duration);
  void Beep(int n, int duration);
};

Buzzer::Buzzer(int pin_in) {
  pin = pin_in;
  pinMode(pin, OUTPUT);
  digitalWrite(pin, LOW);
}

void Buzzer::Use(int duration) {
  digitalWrite(pin, HIGH);
  delay(duration);
  digitalWrite(pin, LOW);
}

void Buzzer::Beep(int n, int duration) {

  for (int i = 1; i < n; i++) {

    digitalWrite(pin, HIGH);
    Serial.println("beeep");
    delay(duration);
    digitalWrite(pin, LOW);
    delay(duration);
  }
  digitalWrite(pin, HIGH);
  Serial.println("beeep");
  delay(duration);
  digitalWrite(pin, LOW);
}

// Definicion de clase para motores

class Motor {

private:
  int pinA;
  int pinB;
  int chA;
  int chB;

public:
  Motor(int pinA_in, int pinB_in, int chA_in, int chB_in);
  void Forward(int vel);
  void Backward(int vel);
  void Stop();
};

// Constructor clase motores
Motor::Motor(int pinA_in, int pinB_in, int chA_in, int chB_in) {
  pinA = pinA_in;
  pinB = pinB_in;
  chA = chA_in;
  chB = chB_in;

  ledcSetup(chA, 1000, 8);
  ledcSetup(chB, 1000, 8);
  ledcAttachPin(pinA, chA);
  ledcAttachPin(pinB, chB);
}

// Metodos motores
void Motor::Forward(int vel) {
  ledcWrite(chA, vel);
  ledcWrite(chB, 0);
}
void Motor::Backward(int vel) {
  ledcWrite(chA, 0);
  ledcWrite(chB, vel);
}
void Motor::Stop() {
  ledcWrite(chA, 0);
  ledcWrite(chB, 0);
}

// Definicion de clase para sensores Sharp
class Sharp {

private:
  int pin;

public:
  Sharp(int pin_in);
  int ReadDigital(int samples);
};

Sharp::Sharp(int pin_in) {
  pin = pin_in;
}

int Sharp::ReadDigital(int samples) {
  int sum = 0;
  int value = 0;
  for (int i = 0; i <= samples; i++) {
    value = analogRead(pin);
    sum += map(value, 200, 3000, 0, 100);
  }
  Serial.println(sum / samples);
  if (sum / samples > 20)
    return YES;
  else
    return NO;
}


class Button {

private:
  int pin;

public:
  Button(int pin_in);
  int is_pressed();
  void wait_pressing();
};

// Constructor clase Button
Button::Button(int pin_in) {
  pin = pin_in;
  pinMode(pin, INPUT);
}

int Button::is_pressed() {
  return digitalRead(pin);
}

void Button::wait_pressing() {
  while (digitalRead(pin) == NO)
    continue;
}

// Definicion de clase PID
class PID {

private:
  int map_start, map_end;
  int color_deadline = 1600;
  int values_read[CNY70_CANT];
  int max_value_read[CNY70_CANT];
  int min_value_read[CNY70_CANT];
  int Cny70_pins[8] = { SENSOR_1, SENSOR_2, SENSOR_3, SENSOR_4, SENSOR_5, SENSOR_6, SENSOR_7, SENSOR_8 };

public:
  PID();
  void Initialize_readings();
  void Calibrate();
  int Read_floor();
  int read_tatami_color();
};

// Constructor clase motores
PID::PID() {
}

int PID::read_tatami_color() {


  if (analogRead(left_CNY) > color_deadline || analogRead(right_CNY) > color_deadline) {
    return BLACK;
  } else {
    return WHITE;
  }
}

void PID::Initialize_readings() {

  for (int i = 0; i < CNY70_CANT; i++) {
    max_value_read[i] = 3500;
    min_value_read[i] = 3500;
  }
}

void PID::Calibrate() {

  int i;

  for (i = 0; i < CNY70_CANT; i++) {
    int value = analogRead(Cny70_pins[i]);
    min_value_read[i] = constrain(min_value_read[i], -100000, value);
    max_value_read[i] = constrain(max_value_read[i], value, 100000);
  }
  if (DEBUG) {
    //Serial.println("CNY_%d: %d, %d ", i, min_value_read[i], max_value_read[i]);
  }
}

int PID::Read_floor() {

  for (int i = 0; i < 4; i++) {
    values_read[i] = analogRead(Cny70_pins[i]);
    values_read[i] = map(values_read[i], min_value_read[i], max_value_read[i], 1000, 0);
    values_read[i] = constrain(values_read[i], 0, 1000);
    //Serial.println(values_read[i]);
  }

  Serial.println();
  for (int i = 4; i < 8; i++) {
    values_read[i] = analogRead(Cny70_pins[i]);
    values_read[i] = map(values_read[i], min_value_read[i], max_value_read[i], 0, 1000);
    values_read[i] = constrain(values_read[i], 0, 1000);
    //Serial.println(values_read[i]);
  }



  return (-16 * values_read[0]) + (-8 * values_read[1]) + (-4 * values_read[2]) + (-2 * values_read[3]) + (2 * values_read[4]) + (4 * values_read[5]) + (8 * values_read[6]) + (16 * values_read[7]);

  //return (-16 * values_read[7]) + (-8 * values_read[6]) + (-4 * values_read[5]) + (-2 * values_read[4]) + (2 * values_read[3]) + (4 * values_read[2]) + (8 * values_read[1]) + (16 * values_read[0]);
}

Motor *rightMotor = new Motor(M1A, M1B, 14, 13);
Motor *leftMotor = new Motor(M2A, M2B, 12, 11);
Button *confirm_button = new Button(PUSH_2);
Button *count_button = new Button(PUSH_1);
Sharp *left_sharp = new Sharp(SENSOR_7);
Sharp *right_sharp = new Sharp(SENSOR_8);
Sharp *center_sharp = new Sharp(SENSOR_6);
Sharp *left_side_sharp = new Sharp(SENSOR_1);
Sharp *right_side_sharp = new Sharp(SENSOR_5);
Buzzer *buzzer = new Buzzer(BUZZER);
PID *pid = new PID();

// ------------------ INICIALIZADOR ---------------------------------------------------------------------------

void initialize(void (*category_loop_function)()) {

  confirm_button->wait_pressing();
  Serial.println("iniciando");
  buzzer->Beep(3, 1000);
  Serial.println("Arranque brrr");

  while (true) {
    category_loop_function();
  }
}

// -------------------- VELOCISTA -----------------------------------------------------------------------------

#define VEL_WHITE_FLOOR 100
#define VEL_MIN 80
#define PID_VEL_MIN 110
//#define PID_VEL_MIN 150 pista naba 7seg y pista 2019 7seg
//#define PID_VEL_MIN 220
bool all_white = false;

int right_vel = 0;
int left_vel = 0;

int values_read[CNY70_CANT];
int max_value_read[CNY70_CANT];
int min_value_read[CNY70_CANT];

void Motor_control(int value) {

  if (black_side == LEFT) {

    right_vel = PID_VEL_MIN - value;
    left_vel = PID_VEL_MIN + value;
  } else {
    right_vel = PID_VEL_MIN + value;
    left_vel = PID_VEL_MIN - value;
  }

  right_vel = constrain(right_vel, 0, 255);
  left_vel = constrain(left_vel, 0, 255);

  Serial.println(left_vel);
  Serial.println(right_vel);

  if (all_white) {

    if (black_side == RIGHT) {

      leftMotor->Forward(0);
      rightMotor->Forward(VEL_WHITE_FLOOR);
    } else {
      rightMotor->Forward(0);
      leftMotor->Forward(VEL_WHITE_FLOOR);
    }
  } else {

    if (right_vel < VEL_MIN) rightMotor->Backward(VEL_MIN + (VEL_MIN - right_vel));
    else rightMotor->Forward(right_vel);
    if (left_vel < VEL_MIN) leftMotor->Backward(VEL_MIN + (VEL_MIN - left_vel));
    else leftMotor->Forward(left_vel);
  }
}

float kp = 10;
float kd = 0;
float ki = 0;
int error = 0;
int last_error = 0;
int actual_value = 0;
int integral = 0;
int PID_calc;
float gain = 120;
float pid_max_average = (kp * 15600) + ki * 0 + (kd * (15600 - -15600));
float pid_min_average = (kp * -15600) + ki * 0 + (kd * (-15600 - 15600));


void line_follower_loop() {

  actual_value = pid->Read_floor();
  //Serial.println(actual_value);

  error = actual_value;
  integral += error;
  integral = constrain(integral, -100000, 100000);

  all_white = actual_value < -26000;

  PID_calc = (kp * error + ki * integral + kd * (error - last_error));
  PID_calc = map(PID_calc, pid_min_average, pid_max_average, -1 * gain, gain);

  last_error = error;

  if (actual_value < pid_min_average) pid_min_average = actual_value;
  if (actual_value > pid_max_average) pid_max_average = actual_value;
  //Serial.println("PID");
  Motor_control(PID_calc);
}

void line_follower_setup() {

  Serial.println("en follower");

  //BT.begin("line_follower_debug");

  /*
    xTaskCreatePinnedToCore(
    ReadSensorsFun, // Function to implement the task
    "Task1",        // Name of the task
    4096,           // Stack size in words
    NULL,           // Task input parameter
    0,              // Priority of the task
    &ReadSensors,   // Task handle.
    0);             // Core where the task should run
  */

  pid->Initialize_readings();

  Serial.println("CALIBRANDO, select");

  while (count_button->is_pressed() == NO) {
    pid->Calibrate();
  }

  Serial.println("Calibrado");

  initialize(line_follower_loop);
}

// -------------------- SUMO RC -------------------------------------------------------------------------------
int velocidad, giro;

void radio_controlled_loop() {

  int yAxisValue = PS4.LStickY();
  int xAxisValue = PS4.RStickX();
  int l1 = PS4.L2Value();
  int r2 = PS4.R2Value();

  if (r2 >= 50) {
    velocidad = 250;
    giro = 150;
  }

  if (l1 >= 50) {
    velocidad = 100;
    giro = 50;
  }

  if (r2 < 50 && l1 < 50) {
    velocidad = 170;
    giro = 70;
  }

  if (yAxisValue >= 50) {
    rightMotor->Forward(velocidad);
    leftMotor->Forward(velocidad);

    if (xAxisValue >= 50) {

      leftMotor->Forward(velocidad);
      rightMotor->Forward(giro);

    }

    else if (xAxisValue <= -50) {

      leftMotor->Forward(giro);
      rightMotor->Forward(velocidad);

    }
  } else if (yAxisValue <= -50)  //Move car Backward
  {
    rightMotor->Backward(velocidad);
    leftMotor->Backward(velocidad);

    if (xAxisValue >= 50) {
      rightMotor->Backward(giro);
      leftMotor->Backward(velocidad);
    } else if (xAxisValue <= -50) {
      rightMotor->Backward(velocidad);
      leftMotor->Backward(giro);
    }
  } else if (xAxisValue >= 50)  //Move car Right
  {
    rightMotor->Backward(150);
    leftMotor->Forward(250);

  } else if (xAxisValue <= -50)  //Move car Left
  {
    rightMotor->Forward(250);
    leftMotor->Backward(150);
  } else  //Stop the car
  {
    rightMotor->Stop();
    leftMotor->Stop();
  }
}

void radio_controlled_setup() {

  PS4.begin();
  while (!PS4.isConnected())
    ;
  buzzer->Use(1000);
  PS4.attach(radio_controlled_loop);
}

// ------------------ DESPEJAR AREA ---------------------------------------------------------------------------


#define LINE_REBOUND_TIME 150
#define TURN_VELOCITY 80
#define TURN_ADJUSTMENT_DIFERENCE 70
#define MAX_VELOCITY 220
#define LIMIT_BLIND_TIME 2500
#define LIMIT_BLIND_ADVANCING_TIME 1000
#define SEEK_VELOCITY 70

int binary_area_cleaner_sum;
int start_seeking_flag = YES;
unsigned long seeking_time;
int saw_right = NO;
int last_value = LEFT;
unsigned long last_rebound_time;
void area_cleaner_loop() {

  if (pid->read_tatami_color() == BLACK) {
    binary_area_cleaner_sum = -1;
  } else {
    binary_area_cleaner_sum = (left_sharp->ReadDigital(10)
                               + center_sharp->ReadDigital(10) * 2
                               + right_sharp->ReadDigital(10) * 4);
  }

  if (right_side_sharp->ReadDigital(10) == YES) saw_right = YES;
  switch (binary_area_cleaner_sum) {

    case -1:

      if (saw_right) {
        last_value = RIGHT;
        saw_right = NO;
      } else {
        last_value = LEFT;
      }
      leftMotor->Backward(100);
      rightMotor->Backward(100);
      delay(700);
      leftMotor->Backward(100);
      rightMotor->Forward(100);
      delay(100);
      last_rebound_time = millis();
      break;

    case 0:  //no ve nada
      /*
            if (start_seeking_flag == YES) {
              seeking_time = millis();
              start_seeking_flag = NO;

            }

            if (millis() > seeking_time + LIMIT_BLIND_TIME) {

              leftMotor->Forward(100);
              rightMotor->Forward(100);

              if (millis() > seeking_time + LIMIT_BLIND_TIME + LIMIT_BLIND_ADVANCING_TIME) start_seeking_flag == YES;
              else{
      


      */
      if (last_value == LEFT) {
        leftMotor->Backward(SEEK_VELOCITY);
        rightMotor->Forward(SEEK_VELOCITY);
      } else {
        leftMotor->Forward(SEEK_VELOCITY);
        rightMotor->Backward(SEEK_VELOCITY);
      }

      if (millis() > last_rebound_time + 5000) {
        while (pid->read_tatami_color() == WHITE) {
          leftMotor->Forward(130);
          rightMotor->Forward(200);
        }
      }
      //}
      // }

      break;

    case 1:
    case 3:
      last_value = LEFT;
      leftMotor->Forward(TURN_VELOCITY);
      rightMotor->Forward(TURN_VELOCITY + TURN_ADJUSTMENT_DIFERENCE);
      break;

    case 4:
    case 6:
      last_value = RIGHT;
      leftMotor->Forward(TURN_VELOCITY + TURN_ADJUSTMENT_DIFERENCE);
      rightMotor->Forward(TURN_VELOCITY);
      break;

    case 8:
      leftMotor->Backward(TURN_VELOCITY + TURN_ADJUSTMENT_DIFERENCE);
      rightMotor->Backward(TURN_VELOCITY);
      break;

    default:
      leftMotor->Forward(MAX_VELOCITY);
      rightMotor->Forward(MAX_VELOCITY);
      break;
  }
}


void area_cleaner_setup() {
  last_rebound_time = millis();
  initialize(area_cleaner_loop);
}
// Funciones para seleccion e inicializacion de modos

void mode_selection() {

  int counter = 0;

  while (confirm_button->is_pressed() == NO) {

    if (count_button->is_pressed() == YES) {

      counter++;
      if (counter > 4)
        counter = 1;

      buzzer->Beep(counter, 100);
      //Serial.println("Counter %f", counter);
      delay(100);
    }
  }
  switch (counter) {

    case 1:
      black_side = LEFT;
      line_follower_setup();
      Serial.println("seguidor de linea");

      break;

    case 2:
      black_side = RIGHT;
      line_follower_setup();
      Serial.println("line follower");

      break;

    case 3:
      area_cleaner_setup();
      Serial.println("area cleaner");

      break;

    case 4:
      radio_controlled_setup();
      Serial.println("radio_control");

      break;
  }
}

void setup() {
  Serial.begin(115200);
  if (DEBUG) Serial.println("inicio programa");
  mode_selection();
}

void loop() {
}

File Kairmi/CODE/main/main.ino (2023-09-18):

#include <PS4Controller.h>
#include <BluetoothSerial.h>
#include "motor.h"

// last commit: arregle rebote trasero 

BluetoothSerial BT;

#define DEBUG 0
#define BT_DEBUG 0
#define DEBUG_VEL 0
// Motores
#define M2A 22
#define M2B 23
#define M1B 19
#define M1A 21

// Sensores
#define SENSOR_2 27
#define SENSOR_3 26
#define SENSOR_1 13
#define SENSOR_4 25
#define SENSOR_5 34
#define SENSOR_6 35
#define SENSOR_7 32
#define SENSOR_8 33

#define LEFT_CNY 27
#define RIGHT_CNY 25
#define BACK_CNY 26

int Cny70_pins[] = {SENSOR_1, SENSOR_2, SENSOR_3, SENSOR_4, SENSOR_5, SENSOR_6, SENSOR_7, SENSOR_8};

#define CNY70_CANT 8

// Control
#define BUZZER 18
#define PUSH_1 16
#define PUSH_2 17

// Constantes

#define BLACK 1
#define WHITE 0
#define YES 1
#define NO 0
#define LEFT 1
#define RIGHT 2

int black_side = BLACK;

class Buzzer
{

private:
  int pin;

public:
  Buzzer(int pin);
  void Use(int duration);
  void Beep(int n, int duration);
};

Buzzer::Buzzer(int pin_in)
{
  pin = pin_in;
  pinMode(pin, OUTPUT);
  digitalWrite(pin, LOW);
}

void Buzzer::Use(int duration)
{
  digitalWrite(pin, HIGH);
  delay(duration);
  digitalWrite(pin, LOW);
}

void Buzzer::Beep(int n, int duration)
{

  for (int i = 1; i < n; i++)
  {

    digitalWrite(pin, HIGH);
    if (DEBUG)
    {
      Serial.println("beeep");
    }
    delay(duration);
    digitalWrite(pin, LOW);
    delay(duration);
  }
  digitalWrite(pin, HIGH);
  if (DEBUG)
  {
    Serial.println("beeep");
  }
  delay(duration);
  digitalWrite(pin, LOW);
}

// Definicion de clase para motores

// Definicion de clase para sensores Sharp

#define MIN_READING 200
#define MAX_READING 3000
#define MIN_MAP 0
#define MAX_MAP 100

class Sharp
{

private:
  int pin;

public:
  Sharp(int pin_in);
  int ReadDigital(int samples, int distance_deadline);
};

Sharp::Sharp(int pin_in)
{
  pin = pin_in;
}

int Sharp::ReadDigital(int samples, int distance_deadline)
{

  int sum = 0;
  int reading = 0;

  for (int i = 0; i < samples; i++)
  {
    reading = analogRead(pin);
    sum += map(reading, MIN_READING, MAX_READING, MIN_MAP, MAX_MAP);
  }

  int average = sum / samples;
  if (DEBUG)
  {
    Serial.println(average);
  }
  return average > distance_deadline;
}

class Button
{

private:
  int pin;
  int cant_pin;

public:
  Button(int pin_in);
  int IsPressed();
  void WaitPressing();
};

// Constructor clase Button
Button::Button(int pin_in)
{
  pin = pin_in;
  pinMode(pin, INPUT);
}

int Button::IsPressed()
{
  return digitalRead(pin);
}

void Button::WaitPressing()
{
  while (digitalRead(pin) == NO)
  {
    continue;
  }
}

// Definicion de clase PID

#define LIMIT_LEN 8

class CNY
{

private:
  int map_min = 0;
  int map_max = 1000;
  int cant_pins;
  int value;
  int values_read[LIMIT_LEN];
  int max_value_read[LIMIT_LEN];
  int min_value_read[LIMIT_LEN];
  int Cny70_pins[LIMIT_LEN];

public:
  CNY(int cny70_pins_in[], int cant);
  void InitializeReadings();
  void Calibrate();
  int ReadFloor();
  int ReadTatamiColor();
  int color_deadline = 500;
};

CNY::CNY(int cny70_pins_in[], int cant)
{

  cant_pins = cant;
  for (int i = 0; i < cant_pins; ++i)
  {
    Cny70_pins[i] = cny70_pins_in[i];
  }
}

void CNY::InitializeReadings()
{

  for (int i = 0; i < cant_pins; i++)
  {
    max_value_read[i] = -10000;
    min_value_read[i] = 10000;
  }
}

void CNY::Calibrate()
{

  for (int i = 0; i < cant_pins; i++)
  {
    int value = analogRead(Cny70_pins[i]);
    if (value < min_value_read[i])
      min_value_read[i] = value;
    else if (value > max_value_read[i])
      max_value_read[i] = value;
  }
  if (DEBUG)
  {
    // Serial.println("CNY_%d: %d, %d ", i, min_value_read[i], max_value_read[i]);
  }
}

int CNY::ReadFloor()
{

  for (int i = 0; i < cant_pins / 2; i++)
  {
    values_read[i] = analogRead(Cny70_pins[i]);
    values_read[i] = map(values_read[i], min_value_read[i], max_value_read[i], map_max, map_min);
    values_read[i] = constrain(values_read[i], map_min, map_max);
    // Serial.println(values_read[i]);
  }

  Serial.println();
  for (int i = cant_pins / 2; i < cant_pins; i++)
  {
    values_read[i] = analogRead(Cny70_pins[i]);
    values_read[i] = map(values_read[i], min_value_read[i], max_value_read[i], map_min, map_max);
    values_read[i] = constrain(values_read[i], map_min, map_max);
    // Serial.println(values_read[i]);
  }

  return (-16 * values_read[0]) + (-8 * values_read[1]) + (-4 * values_read[2]) + (-2 * values_read[3]) + (2 * values_read[4]) + (4 * values_read[5]) + (8 * values_read[6]) + (16 * values_read[7]);

  // return (-16 * values_read[7]) + (-8 * values_read[6]) + (-4 * values_read[5]) + (-2 * values_read[4]) + (2 * values_read[3]) + (4 * values_read[2]) + (8 * values_read[1]) + (16 * values_read[0]);
}

int CNY::ReadTatamiColor()
{
  int value;
  int detected = WHITE;
  for (int i = 0; i < cant_pins; i++)
  {
    value = analogRead(Cny70_pins[i]);

    value = map(value, min_value_read[i], max_value_read[i], map_min, map_max);
    if (value > color_deadline)
    {
      detected = Cny70_pins[i];
    }
  }
  return detected;
}

// Creacion de objetos

Motor rightMotor(M1A, M1B, 14, 13);
Motor leftMotor(M2A, M2B, 12, 11);
Button *confirm_button = new Button(PUSH_2);
Button *count_button = new Button(PUSH_1);
Sharp *left_sharp = new Sharp(SENSOR_8);
Sharp *right_sharp = new Sharp(SENSOR_5);
Sharp *center_sharp = new Sharp(SENSOR_7);
Sharp *left_side_sharp = new Sharp(SENSOR_1);
Sharp *right_side_sharp = new Sharp(SENSOR_6);
Buzzer *buzzer = new Buzzer(BUZZER);
int line_follower_array[] = {SENSOR_1, SENSOR_2, SENSOR_3, SENSOR_4, SENSOR_5, SENSOR_6, SENSOR_7, SENSOR_8};
int area_cleaner_array[] = {LEFT_CNY, RIGHT_CNY};
CNY *line_follower = new CNY(line_follower_array, 8);
CNY *area_cleaner = new CNY(area_cleaner_array, 2);

// ------------------ INICIALIZADOR ---------------------------------------------------------------------------

void initialize(void (*category_loop_function)())
{

  confirm_button->WaitPressing();
  if (DEBUG)
  {
    Serial.println("iniciando");
  }
  buzzer->Beep(3, 1000);
  if (DEBUG)
  {
    Serial.println("Arranque brrr");
  }

  while (true)
  {
    category_loop_function();
  }
}

// -------------------- VELOCISTA -----------------------------------------------------------------------------

#define VEL_WHITE_FLOOR 150
#define COMPENSATION_DEADLINE 80
int PID_VEL_MIN = 200;
bool all_white = false;
int in_straight = YES;
int right_vel = 0;
int left_vel = 0;
int base_velocity = PID_VEL_MIN;
unsigned long time_stamp;
int values_read[CNY70_CANT];
int max_value_read[CNY70_CANT];
int min_value_read[CNY70_CANT];
float kp = 10;
float kd = 4;
float ki = 0;
int error = 0;
int last_error = 0;
int actual_value = 0;
int integral = 0;
int PID_calc;
float gain = 120;
float pid_max_average = (kp * 15600) + ki * 0 + (kd * (15600 - -15600));
float pid_min_average = (kp * -15600) + ki * 0 + (kd * (-15600 - 15600));
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

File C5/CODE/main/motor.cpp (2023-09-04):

#include "motor.h"
#include "Arduino.h"
#include <esp32-hal.h>

Motor::Motor(int pin_a_in, int pin_b_in, int ch_a_in, int ch_b_in) {
  pin_a = pin_a_in;
  pin_b = pin_b_in;
  ch_a = ch_a_in;
  ch_b = ch_b_in;

  ledcSetup(ch_a, frequency, resolution);
  ledcSetup(ch_b, frequency, resolution);
  ledcAttachPin(pin_a, ch_a);
  ledcAttachPin(pin_b, ch_b);
}

// Metodos motores
void Motor::Forward(int vel) {
  ledcWrite(ch_a, vel);
  ledcWrite(ch_b, 0);
}
void Motor::Backward(int vel) {
  ledcWrite(ch_a, 0);
  ledcWrite(ch_b, vel);
}
void Motor::Stop() {
  ledcWrite(ch_a, 0);
  ledcWrite(ch_b, 0);
}

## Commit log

2023-04-26 Fueron agregados los archivos 3D del robot junto a los diseños PCB y el codigo del menu
    [18650_Holder.SLDPRT, Abrazadera_motores_APYS.SLDPRT, BTS7960.SLDPRT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]
2023-05-06 Elimine Backups incesesarios de los PCB's y agregue el codigo de pruebas de motores
2023-05-14 Arregle el Diseño 3D del techo
    [Tapa_B2023.SLDPRT]
2023-07-02 Creacion de los Codigos de Velocista, Quita obstaculos y SumoRC
    [Estrella_Tapa.SLDPRT, Soporte_Alimentacion.SLDPRT, Soporte_motores_APYS_IZQ.SLDPRT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]
2023-07-18 Nuevo Diseño de la tapa y arreglo del soporte del sensor del medio
    [Soporte_SensorMedio.SLDPRT, Tapa_B2023.SLDPRT]
2023-07-21 Añadido codigo 4/7 y Motor_class
2023-08-06 Organize folders
    [18650_Holder.SLDPRT, Abrazadera_motores_APYS.SLDPRT, BTS7960.SLDPRT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]
2023-08-06 Add C5 folders
    [18650_Holder.SLDPRT, Abrazadera_motores_APYS.SLDPRT, BTS7960.SLDPRT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]
2023-08-07 Add calibrate area cleaner
2023-08-09 Add AC calibrate & Debug mode_selection
2023-09-04 Move motor module to main
2023-09-04 Add pin verification script
2023-09-04 Add saw right case & Clean code
2023-09-18 chore: se agrego enum para los swich case y el codigo de navarimi
2023-09-18 chore: fix print mode
    [main.ino]
2023-09-18 More DA velocity
